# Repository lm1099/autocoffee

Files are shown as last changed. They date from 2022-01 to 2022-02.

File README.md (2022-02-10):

# SDP DT05 - AutoCoffee

## To-do
- Add power headers
- Layout main PCB
- Finish power PCB schematic

## Done
- Voltage regulators (12V to 5V, 3.3V)
- GPIO headers
- HM-10 BLE module
- LCD module
- DS3231 RTC module
- ISCP programming interface
- DS18B20 temp sensors (x2)
- VL6810X TOF sensors (x4)
- A4988 stepper motor drivers (x6)
- Fan driver (x1)

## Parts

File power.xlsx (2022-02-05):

Bus (V) | Current (A) | Qty | Total (A) | Power (W) | Part
3.3 | 0.5 | 1 | 0.5 | 1.65 | PIC24
3.3 | 0.05 | 1 | 0.05 | 0.165 | HM-10
15 | 0.05 | 1 | 0.05 | 0.75 | LCD
3.3 | 0.01 | 6 | 0.06 | 0.198 | A4988
3.3 | 0.015 | 2 | 0.03 | 0.099 | VL6180X
12 | 9.31392 | 3 | 27.94176 | 335.30112 | Stepper Motors (x6)
12 | 0.6 | 1 | 0.6 | 7.2 | Water pump
12 | 1 | 1 | 1 | 12 | Fan

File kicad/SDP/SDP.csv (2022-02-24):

Source: | C:\Users\Landon\Documents\University of Akron\SDP\autocoffee\kicad\SDP\SDP.kicad_sch
Date: | 2/22/2022 9:56:27 AM
Tool: | Eeschema (6.0.2)
Generator: | C:\Program Files\KiCad\6.0\bin\scripting\plugins/bom_csv_grouped_by_value_with_fp.py
Component Count: | 105
Ref | Qnty | Value | Cmp name | Footprint | Description | Vendor
B1, | 1 | 1056 | 1056 | Keystone_1056:1056
C1, C27, | 2 | 10u | C_Small | Capacitor_SMD:C_0805_2012Metric | Unpolarized capacitor, small symbol
C2, C3, C4, C5, C6, C7, | 6 | 0.1u | C_Small | Capacitor_SMD:C_0603_1608Metric | Unpolarized capacitor, small symbol
C8, C14, | 2 | 10u | C_Small | Capacitor_SMD:C_1206_3216Metric | Unpolarized capacitor, small symbol
C9, C15, C16, | 3 | 220p | C_Small | Capacitor_SMD:C_0805_2012Metric | Unpolarized capacitor, small symbol
C10, | 1 | 56p | C_Small | Capacitor_SMD:C_0805_2012Metric | Unpolarized capacitor, small symbol
C11, C17, | 2 | 0.015u | C_Small | Capacitor_SMD:C_0805_2012Metric | Unpolarized capacitor, small symbol
C12, C18, C22, C23, C26, | 5 | 0.1u | C_Small | Capacitor_SMD:C_0805_2012Metric | Unpolarized capacitor, small symbol
C13, | 1 | 330u | C_Polarized_Small_US | EEETG1C331UP:EEETG1C331UP | Polarized capacitor, small US symbol
C19, | 1 | 470u | C_Polarized_Small_US | EEVTG1C471Q:EEVTG1C471Q | Polarized capacitor, small US symbol
C20, C21, | 2 | 27p | C_Small | Capacitor_SMD:C_0805_2012Metric | Unpolarized capacitor, small symbol
C24, C25, | 2 | 15p | C_Small | Capacitor_SMD:C_0805_2012Metric | Unpolarized capacitor, small symbol
C39, | 1 | 47u | C_Small | Capacitor_THT:C_Radial_D8.0mm_H11.5mm_P3.50mm | Unpolarized capacitor, small symbol
C40, | 1 | 220u | C_Small | Capacitor_THT:C_Radial_D10.0mm_H16.0mm_P5.00mm | Unpolarized capacitor, small symbol
D1, D5, | 2 | Green | LED_Small | LED_SMD:LED_0805_2012Metric | Light emitting diode, small symbol
D2, | 1 | 1SMA5927BT3G | D_Zener_Small | Diode_SMD:D_SMA | Zener diode, small symbol
D3, D4, | 2 | CDBA240-G | D_Schottky_Small | Diode_SMD:D_SMA | Schottky diode, small symbol
F1, | 1 | 2A | Polyfuse_Small | Fuse:Fuse_1206_3216Metric | Resettable fuse, polymeric positive temperature coefficient, small symbol
H1, H2, H3, H4, | 4 | MountingHole_Pad | MountingHole_Pad | MountingHole:MountingHole_3.2mm_M3_Pad | Mounting Hole with connection
J1, | 1 | GPIO | Conn_02x07_Odd_Even | Connector_PinSocket_2.54mm:PinSocket_2x07_P2.54mm_Vertical | Generic connector, double row, 02x07, odd/even pin numbering scheme (row 1 odd numbers, row 2 even numbers), script generated (kicad-library-utils/schlib/autogen/connector/)
J2, J13, J14, J15, J16, J17, | 6 | Conn_01x03 | Conn_01x03 | Connector_PinSocket_2.54mm:PinSocket_1x03_P2.54mm_Vertical | Generic connector, single row, 01x03, script generated (kicad-library-utils/schlib/autogen/connector/)
J3, | 1 | UART | Conn_02x04_Odd_Even | Connector_PinSocket_2.54mm:PinSocket_2x04_P2.54mm_Vertical | Generic connector, double row, 02x04, odd/even pin numbering scheme (row 1 odd numbers, row 2 even numbers), script generated (kicad-library-utils/schlib/autogen/connector/)
J4, | 1 | I2C1 | Conn_01x02 | Connector_PinSocket_2.54mm:PinSocket_1x02_P2.54mm_Vertical | Generic connector, single row, 01x02, script generated (kicad-library-utils/schlib/autogen/connector/)
J5, J6, J25, | 3 | Conn_01x04 | Conn_01x04 | Connector_PinSocket_2.54mm:PinSocket_1x04_P2.54mm_Vertical | Generic connector, single row, 01x04, script generated (kicad-library-utils/schlib/autogen/connector/)
J7, | 1 | RJ25 | RJ25 | 5555165-1:TE_5555165-1 | RJ connector, 6P6C (6 positions 6 connected)
J8, J9, J11, J12, | 4 | Conn_01x07 | Conn_01x07 | Connector_PinSocket_2.54mm:PinSocket_1x07_P2.54mm_Vertical | Generic connector, single row, 01x07, script generated (kicad-library-utils/schlib/autogen/connector/)
J10, | 1 | Limit | Conn_02x06_Odd_Even | Connector_PinHeader_2.54mm:PinHeader_2x06_P2.54mm_Vertical | Generic connector, double row, 02x06, odd/even pin numbering scheme (row 1 odd numbers, row 2 even numbers), script generated (kicad-library-utils/schlib/autogen/connector/)
J18, | 1 | 12V | Conn_02x02_Odd_Even | Connector_PinSocket_2.54mm:PinSocket_2x02_P2.54mm_Vertical | Generic connector, double row, 02x02, odd/even pin numbering scheme (row 1 odd numbers, row 2 even numbers), script generated (kicad-library-utils/schlib/autogen/connector/)
J19, | 1 | I2C2 | Conn_01x02 | Connector_PinSocket_2.54mm:PinSocket_1x02_P2.54mm_Vertical | Generic connector, single row, 01x02, script generated (kicad-library-utils/schlib/autogen/connector/)
J20, | 1 | POWER | Conn_01x02 | Connector_PinSocket_2.54mm:PinSocket_1x02_P2.54mm_Vertical | Generic connector, single row, 01x02, script generated (kicad-library-utils/schlib/autogen/connector/)
J24, | 1 | POWER | Conn_02x07_Odd_Even | Connector_PinSocket_2.54mm:PinSocket_2x07_P2.54mm_Vertical | Generic connector, double row, 02x07, odd/even pin numbering scheme (row 1 odd numbers, row 2 even numbers), script generated (kicad-library-utils/schlib/autogen/connector/)
J26, | 1 | Conn_01x02 | Conn_01x02 | TerminalBlock_Phoenix:TerminalBlock_Phoenix_PT-1,5-2-5.0-H_1x02_P5.00mm_Horizontal | Generic connector, single row, 01x02, script generated (kicad-library-utils/schlib/autogen/connector/)
J27, | 1 | MOTOR | Conn_02x08_Odd_Even | Connector_PinSocket_2.54mm:PinSocket_2x08_P2.54mm_Vertical | Generic connector, double row, 02x08, odd/even pin numbering scheme (row 1 odd numbers, row 2 even numbers), script generated (kicad-library-utils/schlib/autogen/connector/)
L1, L3, | 2 | 22u | L_Small | DR125-220-R:DR125-220-R | Inductor, small symbol
L2, | 1 | 15u | L_Small | Inductor_SMD:L_12x12mm_H8mm | Inductor, small symbol
MOSFET1, | 1 | SSM3J334R_LFT | SSM3J334R_LFT | Package_TO_SOT_SMD:SOT-23
R1, R7, | 2 | 332k | R_Small | Resistor_SMD:R_0805_2012Metric | Resistor, small symbol
R2, R4, R16, R17, R20, R21, R22, R23, R24, R25, | 10 | 10k | R_Small | Resistor_SMD:R_0805_2012Metric | Resistor, small symbol
R3, R9, | 2 | 68.1k | R_Small | Resistor_SMD:R_0805_2012Metric | Resistor, small symbol
R5, | 1 | 1.91k | R_Small | Resistor_SMD:R_0805_2012Metric | Resistor, small symbol
R6, | 1 | 40.2k | R_Small | Resistor_SMD:R_0805_2012Metric | Resistor, small symbol
R8, | 1 | 10.2k | R_Small | Resistor_SMD:R_0805_2012Metric | Resistor, small symbol
R10, | 1 | 3.3k | R_Small | Resistor_SMD:R_0805_2012Metric | Resistor, small symbol
R11, | 1 | 30.9k | R_Small | Resistor_SMD:R_0805_2012Metric | Resistor, small symbol
R12, R13, R14, R15, R19, | 5 | 2k2 | R_Small | Resistor_SMD:R_0805_2012Metric | Resistor, small symbol
R18, R47, | 2 | 50k | R_Small | Resistor_SMD:R_0805_2012Metric | Resistor, small symbol
R48, | 1 | 1k | R_Small | Resistor_SMD:R_0805_2012Metric | Resistor, small symbol
R49, | 1 | 0.68 | R_Small | Resistor_SMD:R_0805_2012Metric | Resistor, small symbol
SW1, | 1 | SW_Push_Dual | SW_Push_Dual | 1825910-6:SW_1825910-6-4 | Push button switch, generic, symbol, four pins
TP1, TP2, | 2 | TestPoint_Small | TestPoint_Small | TestPoint:TestPoint_Keystone_5005-5009_Compact | test point
U1, U2, | 2 | TPS54233 | TPS54233 | Package_SO:SOIC-8_3.9x4.9mm_P1.27mm | 2A, Step Down DC-DC Converter with Eco-mode, 3.5-28V Input Voltage, SO-8
U3, | 1 | PIC24FJ128GA010-I/PT | PIC24FJ128GA010-I{slash}PT | PIC24FJ128GA010-I-PT:PIC24FJ128GA010-I&slash_PT
U4, | 1 | DS3231SN-T&R | DS3231SN-T&R_1 | DS3231SN:DS3231SN-T&R
Y1, | 1 | 8MHz | Crystal_Small | ECS-80-20-5PXDU-TR:XTAL_ECS-80-20-5PXDU-TR | Two pin crystal, small symbol
Y2, | 1 | 32.768kHz | Crystal_Small | Crystal:Crystal_DS26_D2.0mm_L6.0mm_Horizontal | Two pin crystal, small symbol

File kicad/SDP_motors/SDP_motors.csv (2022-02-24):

Source: | C:\Users\Landon\Documents\University of Akron\SDP\autocoffee\kicad\SDP_motors\SDP_motors.kicad_sch
Date: | 2/23/2022 13:58
Tool: | Eeschema (6.0.2)
Generator: | C:\Program Files\KiCad\6.0\bin\scripting\plugins/bom_csv_grouped_by_value_with_fp.py
Component Count: | 76
Ref | Qnty | Value | Cmp name | Footprint | Description | Vendor
A1, A2, A3, A4, A5, A6, | 6 | Pololu_Breakout_A4988 | Pololu_Breakout_A4988 | Module:Pololu_Breakout-16_15.2x20.3mm | Pololu Breakout Board, Stepper Driver A4988
C1, C2, C3, C4, C5, C6, | 6 | 50TZV100M8X10.5 | 50TZV100M8X10.5 | 50TZV100M8X10:50TZV100M8X10.5
C7, C8, C9, | 3 | 470u | C_Small | Capacitor_THT:C_Radial_D12.5mm_H20.0mm_P5.00mm | Unpolarized capacitor, small symbol
D1, D2, D3, | 3 | SS1200 | 1N4007 | Diode_SMD:D_SMA | 1000V 1A General Purpose Rectifier Diode, DO-41
H1, H2, H3, H4, | 4 | MountingHole_Pad | MountingHole_Pad | MountingHole:MountingHole_3.2mm_M3_Pad | Mounting Hole with connection
J1, J2, J3, J4, J5, J6, | 6 | Conn_01x04 | Conn_01x04 | Connector_PinHeader_2.54mm:PinHeader_1x04_P2.54mm_Vertical | Generic connector, single row, 01x04, script generated (kicad-library-utils/schlib/autogen/connector/)
J7, J8, J9, | 3 | Conn_01x02 | Conn_01x02 | TerminalBlock_Phoenix:TerminalBlock_Phoenix_PT-1,5-2-5.0-H_1x02_P5.00mm_Horizontal | Generic connector, single row, 01x02, script generated (kicad-library-utils/schlib/autogen/connector/)
J10, | 1 | MOTOR | Conn_02x08_Odd_Even | Connector_PinSocket_2.54mm:PinSocket_2x08_P2.54mm_Vertical | Generic connector, double row, 02x08, odd/even pin numbering scheme (row 1 odd numbers, row 2 even numbers), script generated (kicad-library-utils/schlib/autogen/connector/)
JP1, JP4, JP7, JP10, JP13, JP16, | 6 | JP_MS1 | Jumper_2_Open | Jumper:SolderJumper-2_P1.3mm_Open_RoundedPad1.0x1.5mm | Jumper, 2-pole, open
JP2, JP5, JP8, JP11, JP14, JP17, | 6 | JP_MS2 | Jumper_2_Open | Jumper:SolderJumper-2_P1.3mm_Open_RoundedPad1.0x1.5mm | Jumper, 2-pole, open
JP3, JP6, JP9, JP12, JP15, JP18, | 6 | JP_MS3 | Jumper_2_Open | Jumper:SolderJumper-2_P1.3mm_Open_RoundedPad1.0x1.5mm | Jumper, 2-pole, open
Q1, Q2, Q3, | 3 | IRLZ44N | IRLZ44N | Package_TO_SOT_SMD:TO-263-2 | 47A Id, 55V Vds, 22mOhm Rds Single N-Channel HEXFET Power MOSFET, TO-220AB
R1, R2, R3, R4, R7, R8, R9, R10, R13, R14, R15, R16, R19, R20, R21, | 15 | 10k | R_Small | Resistor_SMD:R_0805_2012Metric | Resistor, small symbol
R5, R6, R11, R12, R17, R18, | 6 | 100k | R_Small | Resistor_SMD:R_0805_2012Metric | Resistor, small symbol
TP1, TP2, | 2 | TestPoint_Small | TestPoint_Small | TestPoint:TestPoint_Keystone_5005-5009_Compact | test point

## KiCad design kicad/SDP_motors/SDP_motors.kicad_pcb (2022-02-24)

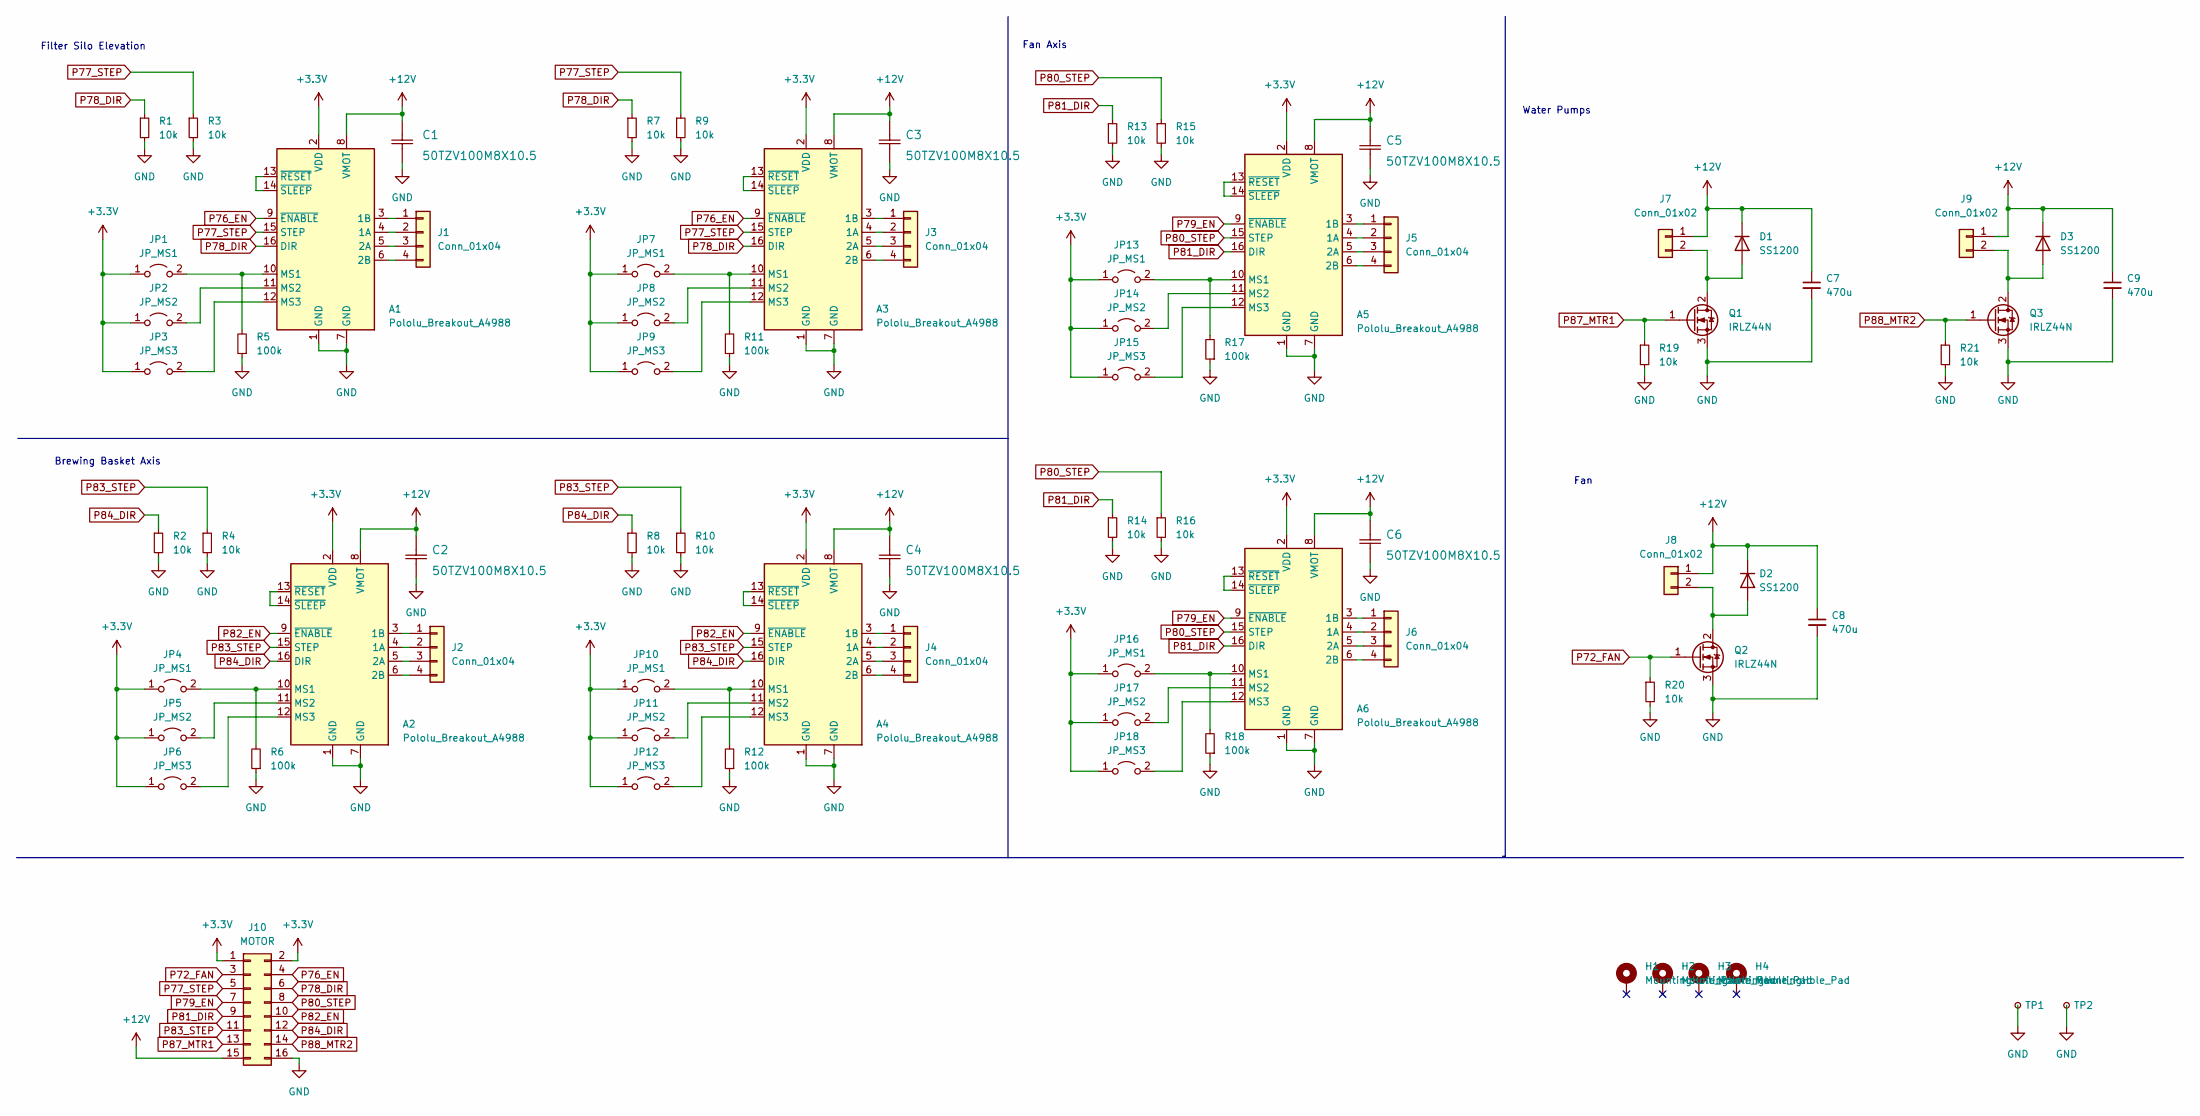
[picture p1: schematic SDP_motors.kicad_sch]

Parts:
A1, A2, A3, A4, A5, A6: Pololu_Breakout_A4988; Pololu_Breakout-16_15.2x20.3mm
C1, C2, C3, C4, C5, C6: 50TZV100M8X10.5
C7, C8, C9: 470u; C_Radial_D12.5mm_H20.0mm_P5.00mm
D1, D2, D3: SS1200; D_SMA
H1, H2, H3, H4: MountingHole_Pad; MountingHole_3.2mm_M3_Pad
J1, J2, J3, J4, J5, J6: Conn_01x04; PinHeader_1x04_P2.54mm_Vertical
J7, J8, J9: Conn_01x02; TerminalBlock_Phoenix_PT-1,5-2-5.0-H_1x02_P5.00mm_Horizontal
J10: MOTOR; PinSocket_2x08_P2.54mm_Vertical
JP1, JP4, JP7, JP10, JP13, JP16: JP_MS1; SolderJumper-2_P1.3mm_Open_RoundedPad1.0x1.5mm
JP2, JP5, JP8, JP11, JP14, JP17: JP_MS2; SolderJumper-2_P1.3mm_Open_RoundedPad1.0x1.5mm
JP3, JP6, JP9, JP12, JP15, JP18: JP_MS3; SolderJumper-2_P1.3mm_Open_RoundedPad1.0x1.5mm
Q1, Q2, Q3: IRLZ44N; TO-263-2
R1, R2, R3, R4, R7, R8, R9, R10, R13, R14, R15, R16, R19, R20, R21: 10k; R_0805_2012Metric
R5, R6, R11, R12, R17, R18: 100k; R_0805_2012Metric
TP1, TP2: TestPoint_Small; TestPoint_Keystone_5005-5009_Compact

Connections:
+3V3: A1.2 (VDD), A2.2 (VDD), A3.2 (VDD), A4.2 (VDD), A5.2 (VDD), A6.2 (VDD), J10.1, J10.2, JP1.1 (A), JP2.1 (A), JP3.1 (A), JP4.1 (A), JP5.1 (A), JP6.1 (A), JP7.1 (A), JP8.1 (A), JP9.1 (A), JP10.1 (A), JP11.1 (A), JP12.1 (A), JP13.1 (A), JP14.1 (A), JP15.1 (A), JP16.1 (A), JP17.1 (A), JP18.1 (A)
+12V: A1.8 (VMOT), A2.8 (VMOT), A3.8 (VMOT), A4.8 (VMOT), A5.8 (VMOT), A6.8 (VMOT), C1.2, C2.2, C3.2, C4.2, C5.2, C6.2, C7.1, C8.1, C9.1, D1.1 (K), D2.1 (K), D3.1 (K), J7.1, J8.1, J9.1, J10.15
GND: A1.1 (GND), A1.7 (GND), A2.1 (GND), A2.7 (GND), A3.1 (GND), A3.7 (GND), A4.1 (GND), A4.7 (GND), A5.1 (GND), A5.7 (GND), A6.1 (GND), A6.7 (GND), C1.1, C2.1, C3.1, C4.1, C5.1, C6.1, C7.2, C8.2, C9.2, J10.16, Q1.3 (S), Q2.3 (S), Q3.3 (S), R1.2, R2.2, R3.2, R4.2, R5.1, R6.1, R7.2, R8.2, R9.2, R10.2, R11.1, R12.1, R13.2, R14.2, R15.2, R16.2, R17.1, R18.1, R19.2, R20.2, R21.2, TP1.1, TP2.1
unnamed: A1.3 (1B), J1.1
unnamed: A1.4 (1A), J1.2
unnamed: A1.5 (2A), J1.3
unnamed: A1.6 (2B), J1.4
unnamed: A1.10 (MS1), JP1.2 (B), R5.2
unnamed: A1.11 (MS2), JP2.2 (B)
unnamed: A1.12 (MS3), JP3.2 (B)
unnamed: A1.13 (~RESET), A1.14 (~SLEEP)
unnamed: A2.3 (1B), J2.1
unnamed: A2.4 (1A), J2.2
unnamed: A2.5 (2A), J2.3
unnamed: A2.6 (2B), J2.4
unnamed: A2.10 (MS1), JP4.2 (B), R6.2
unnamed: A2.11 (MS2), JP5.2 (B)
unnamed: A2.12 (MS3), JP6.2 (B)
unnamed: A2.13 (~RESET), A2.14 (~SLEEP)
unnamed: A3.3 (1B), J3.1
unnamed: A3.4 (1A), J3.2
unnamed: A3.5 (2A), J3.3
unnamed: A3.6 (2B), J3.4
unnamed: A3.10 (MS1), JP7.2 (B), R11.2
unnamed: A3.11 (MS2), JP8.2 (B)
unnamed: A3.12 (MS3), JP9.2 (B)
unnamed: A3.13 (~RESET), A3.14 (~SLEEP)
unnamed: A4.3 (1B), J4.1
unnamed: A4.4 (1A), J4.2
unnamed: A4.5 (2A), J4.3
unnamed: A4.6 (2B), J4.4
unnamed: A4.10 (MS1), JP10.2 (B), R12.2
unnamed: A4.11 (MS2), JP11.2 (B)
unnamed: A4.12 (MS3), JP12.2 (B)
unnamed: A4.13 (~RESET), A4.14 (~SLEEP)
unnamed: A5.3 (1B), J5.1
unnamed: A5.4 (1A), J5.2
unnamed: A5.5 (2A), J5.3
unnamed: A5.6 (2B), J5.4
unnamed: A5.10 (MS1), JP13.2 (B), R17.2
unnamed: A5.11 (MS2), JP14.2 (B)
unnamed: A5.12 (MS3), JP15.2 (B)
unnamed: A5.13 (~RESET), A5.14 (~SLEEP)
unnamed: A6.3 (1B), J6.1
unnamed: A6.4 (1A), J6.2
unnamed: A6.5 (2A), J6.3
unnamed: A6.6 (2B), J6.4
unnamed: A6.10 (MS1), JP16.2 (B), R18.2
unnamed: A6.11 (MS2), JP17.2 (B)
unnamed: A6.12 (MS3), JP18.2 (B)
unnamed: A6.13 (~RESET), A6.14 (~SLEEP)
unnamed: D1.2 (A), J7.2, Q1.2 (D)
unnamed: D2.2 (A), J8.2, Q2.2 (D)
unnamed: D3.2 (A), J9.2, Q3.2 (D)
P72_FAN: J10.3, Q2.1 (G), R20.1
P76_EN: A1.9 (~ENABLE), A3.9 (~ENABLE), J10.4
P77_STEP: A1.15 (STEP), A3.15 (STEP), J10.5, R3.1, R9.1
P78_DIR: A1.16 (DIR), A3.16 (DIR), J10.6, R1.1, R7.1
P79_EN: A5.9 (~ENABLE), A6.9 (~ENABLE), J10.7
P80_STEP: A5.15 (STEP), A6.15 (STEP), J10.8, R15.1, R16.1
P81_DIR: A5.16 (DIR), A6.16 (DIR), J10.9, R13.1, R14.1
P82_EN: A2.9 (~ENABLE), A4.9 (~ENABLE), J10.10
P83_STEP: A2.15 (STEP), A4.15 (STEP), J10.11, R4.1, R10.1
P84_DIR: A2.16 (DIR), A4.16 (DIR), J10.12, R2.1, R8.1
P87_MTR1: J10.13, Q1.1 (G), R19.1
P88_MTR2: J10.14, Q3.1 (G), R21.1

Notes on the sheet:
Filter Silo Elevation
Water Pumps
Fan
Brewing Basket Axis
Fan Axis

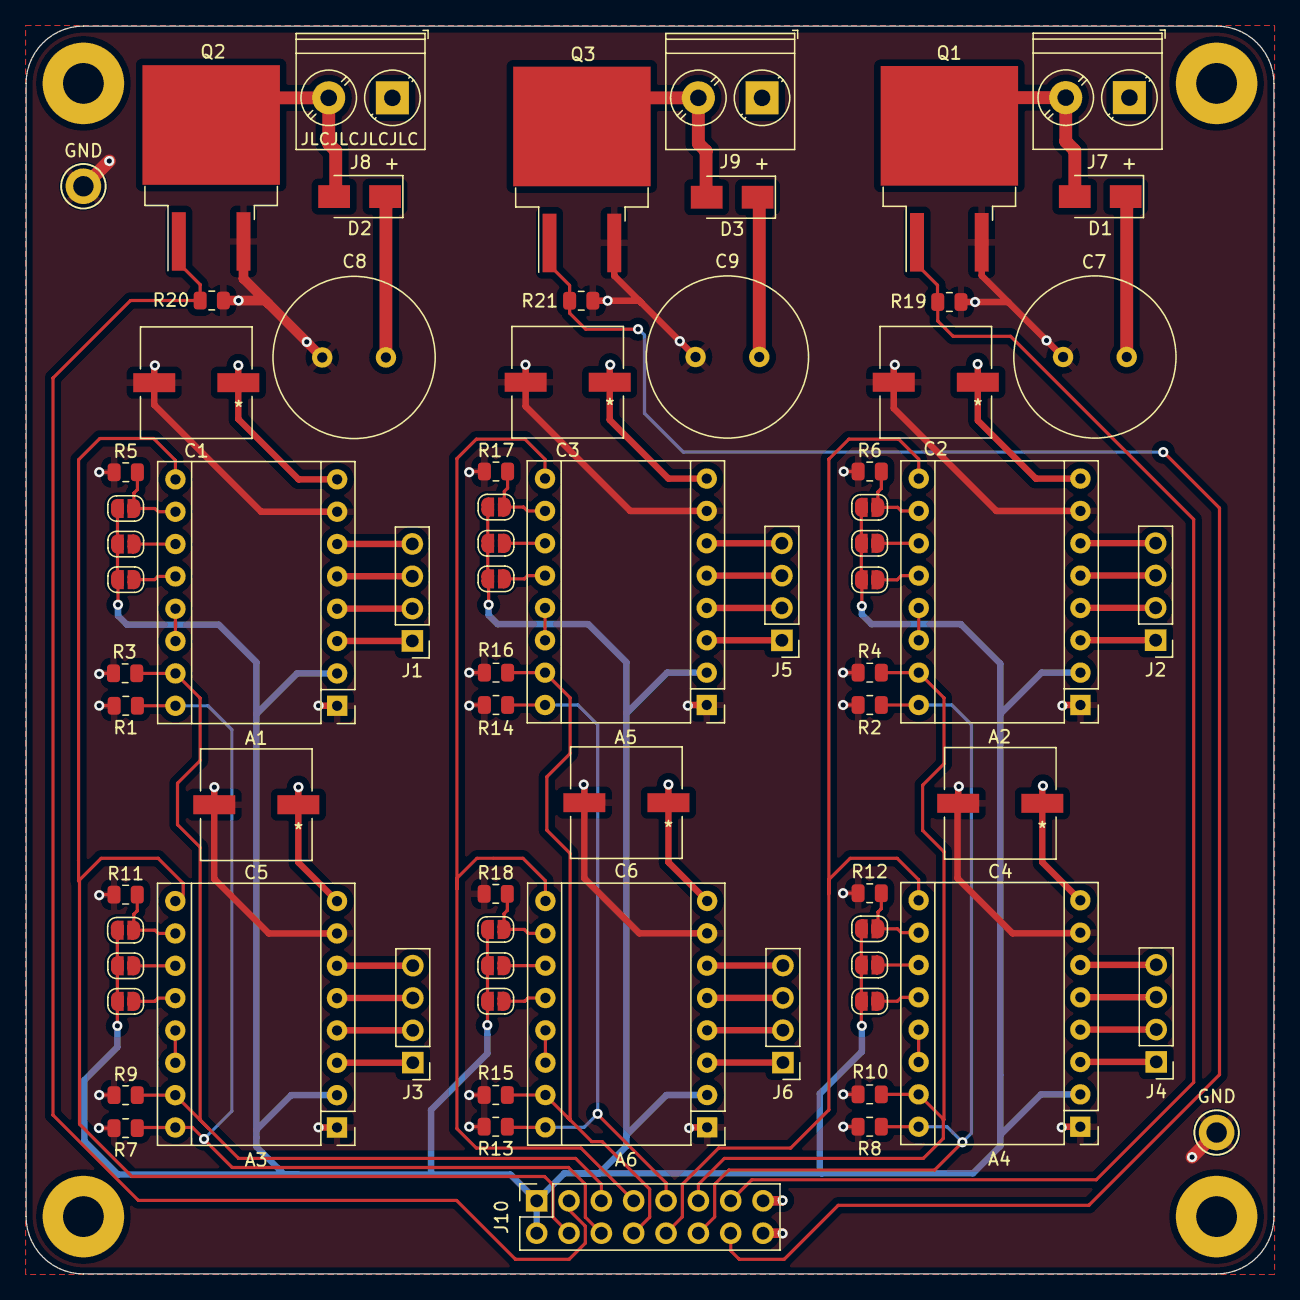
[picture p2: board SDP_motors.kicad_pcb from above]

Board: 4 copper layers, 98.0 x 98.0 mm, 76 parts (0 on the bottom side), 66 nets.

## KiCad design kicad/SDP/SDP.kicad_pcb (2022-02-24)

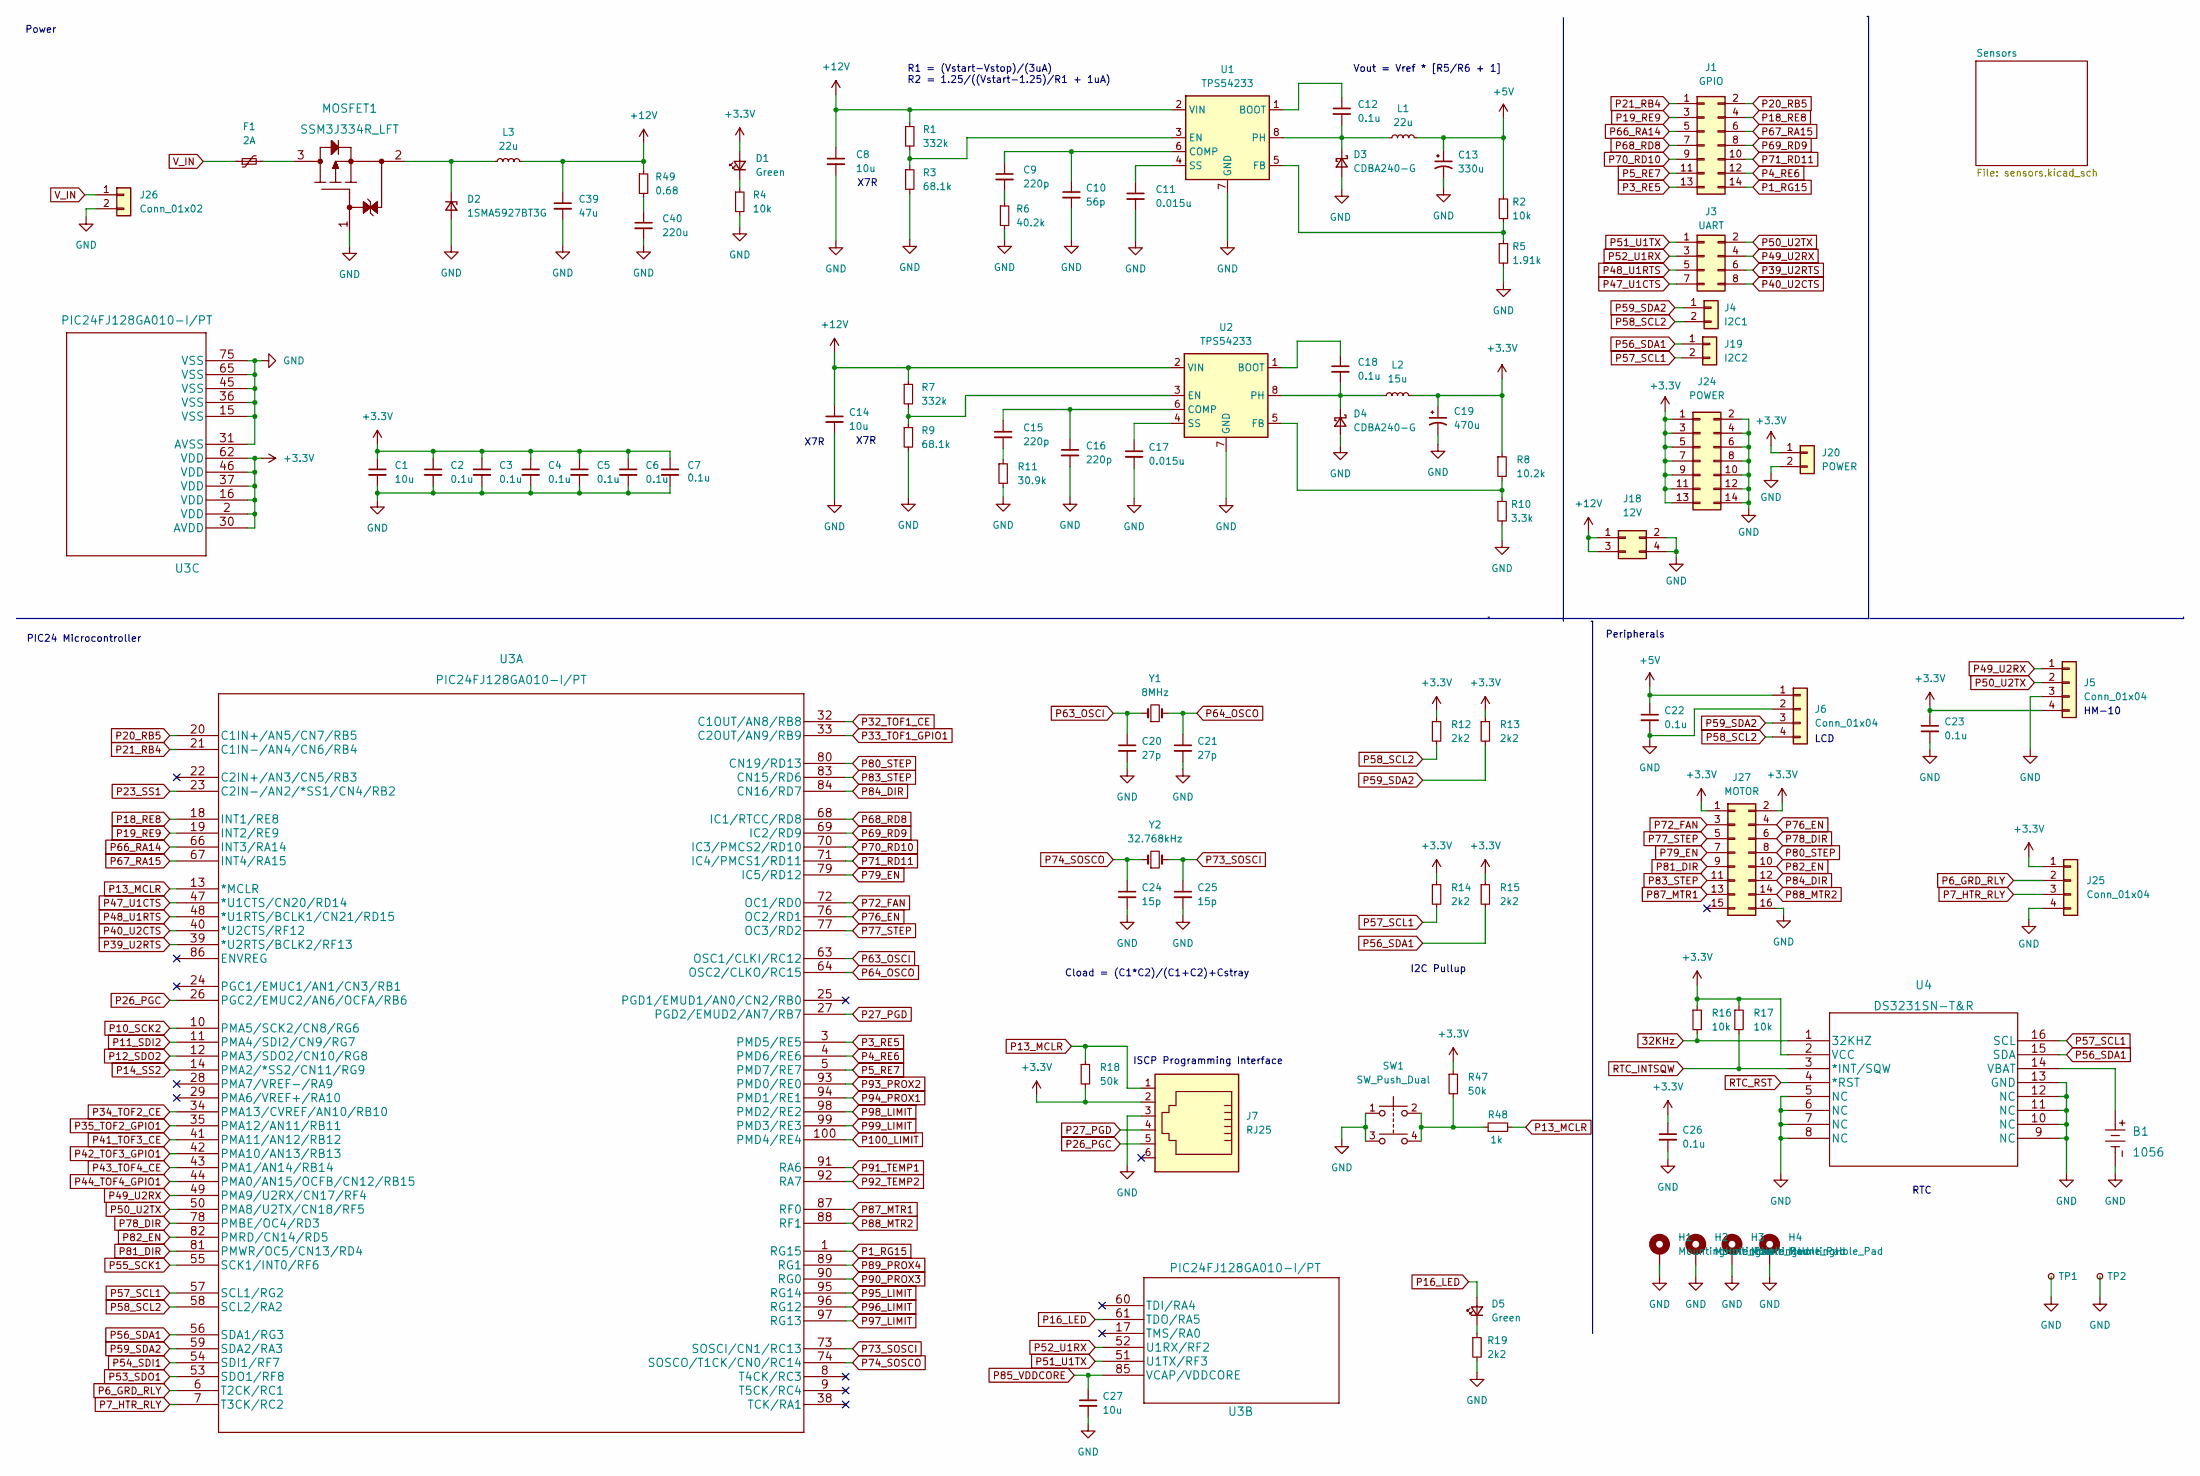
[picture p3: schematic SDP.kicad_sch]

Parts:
B1: 1056
C1, C27: 10u; C_0805_2012Metric
C2, C3, C4, C5, C6, C7: 0.1u; C_0603_1608Metric
C8, C14: 10u; C_1206_3216Metric
C9, C15, C16: 220p; C_0805_2012Metric
C10: 56p; C_0805_2012Metric
C11, C17: 0.015u; C_0805_2012Metric
C12, C18, C22, C23, C26: 0.1u; C_0805_2012Metric
C13: 330u; EEETG1C331UP
C19: 470u; EEVTG1C471Q
C20, C21: 27p; C_0805_2012Metric
C24, C25: 15p; C_0805_2012Metric
C39: 47u; C_Radial_D8.0mm_H11.5mm_P3.50mm
C40: 220u; C_Radial_D10.0mm_H16.0mm_P5.00mm
D1, D5: Green; LED_0805_2012Metric
D2: 1SMA5927BT3G; D_SMA
D3, D4: CDBA240-G; D_SMA
F1: 2A; Fuse_1206_3216Metric
H1, H2, H3, H4: MountingHole_Pad; MountingHole_3.2mm_M3_Pad
J1: GPIO; PinSocket_2x07_P2.54mm_Vertical
J3: UART; PinSocket_2x04_P2.54mm_Vertical
J4: I2C1; PinSocket_1x02_P2.54mm_Vertical
J5, J6, J25: Conn_01x04; PinSocket_1x04_P2.54mm_Vertical
J7: RJ25; TE_5555165-1
J18: 12V; PinSocket_2x02_P2.54mm_Vertical
J19: I2C2; PinSocket_1x02_P2.54mm_Vertical
J20: POWER; PinSocket_1x02_P2.54mm_Vertical
J24: POWER; PinSocket_2x07_P2.54mm_Vertical
J26: Conn_01x02; TerminalBlock_Phoenix_PT-1,5-2-5.0-H_1x02_P5.00mm_Horizontal
J27: MOTOR; PinSocket_2x08_P2.54mm_Vertical
L1, L3: 22u; DR125-220-R
L2: 15u; L_12x12mm_H8mm
MOSFET1: SSM3J334R_LFT; SOT-23
R1, R7: 332k; R_0805_2012Metric
R2, R4, R16, R17: 10k; R_0805_2012Metric
R3, R9: 68.1k; R_0805_2012Metric
R5: 1.91k; R_0805_2012Metric
R6: 40.2k; R_0805_2012Metric
R8: 10.2k; R_0805_2012Metric
R10: 3.3k; R_0805_2012Metric
R11: 30.9k; R_0805_2012Metric
R12, R13, R14, R15, R19: 2k2; R_0805_2012Metric
R18, R47: 50k; R_0805_2012Metric
R48: 1k; R_0805_2012Metric
R49: 0.68; R_0805_2012Metric
SW1: SW_Push_Dual; SW_1825910-6-4
TP1, TP2: TestPoint_Small; TestPoint_Keystone_5005-5009_Compact
U1, U2: TPS54233; SOIC-8_3.9x4.9mm_P1.27mm
U3: PIC24FJ128GA010-I/PT; PIC24FJ128GA010-I&slash_PT
U4: DS3231SN-T&R
Y1: 8MHz; XTAL_ECS-80-20-5PXDU-TR
Y2: 32.768kHz; Crystal_DS26_D2.0mm_L6.0mm_Horizontal

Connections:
32KHz: R16.2, U4.1 (32KHZ)
+3V3: C1.1, C2.1, C3.1, C4.1, C5.1, C6.1, C7.1, C19.1, C23.1, C26.1, D1.2 (A), J5.4, J7.2, J20.1, J24.1, J24.3, J24.5, J24.7, J24.9, J24.11, J24.13, J25.1, J27.1, J27.2, L2.2, R8.1, R12.1, R13.1, R14.1, R15.1, R16.1, R17.1, R18.2, R47.1, U3.2 (VDD), U3.16 (VDD), U3.30 (AVDD), U3.37 (VDD), U3.46 (VDD), U3.62 (VDD), U4.2 (VCC); also elsewhere on the board
+5V: C13.1, C22.1, J6.1, L1.2, R2.1
+12V: C8.1, C14.1, C39.1, J18.1, J18.3, L3.2, R1.1, R7.1, R49.1, U1.2 (VIN), U2.2 (VIN)
GND: B1.1, C1.2, C2.2, C3.2, C4.2, C5.2, C6.2, C7.2, C8.2, C10.2, C11.2, C13.2, C14.2, C16.2, C17.2, C19.2, C20.2, C21.2, C22.2, C23.2, C24.2, C25.2, C26.2, C27.2, C39.2, C40.2, D2.2 (A), D3.2 (A), D4.2 (A), H1.1, H2.1, H3.1, H4.1, J5.3, J6.2, J7.3, J18.2, J18.4, J20.2, J24.2, J24.4, J24.6, J24.8, J24.10, J24.12, J24.14, J25.4, J26.2, J27.16, MOSFET1.1 (GATE), R3.2, R4.2, R5.2, R6.2, R9.2, R10.2, R11.2, R19.2, SW1.1, SW1.3, TP1.1, TP2.1, U1.7 (GND), U2.7 (GND), U3.15 (VSS), U3.31 (AVSS), U3.36 (VSS), U3.45 (VSS), U3.65 (VSS), U3.75 (VSS), U4.5 (NC), U4.6 (NC), U4.7 (NC), U4.8 (NC), U4.9 (NC), U4.10 (NC), U4.11 (NC), U4.12 (NC), U4.13 (GND); also elsewhere on the board
unnamed: B1.2, U4.14 (VBAT)
unnamed: C9.2, R6.1
unnamed: C9.1, C10.1, U1.6 (COMP)
unnamed: C11.1, U1.4 (SS)
unnamed: C12.1, U1.1 (BOOT)
unnamed: C12.2, D3.1 (K), L1.1, U1.8 (PH)
unnamed: C15.1, C16.1, U2.6 (COMP)
unnamed: C15.2, R11.1
unnamed: C17.1, U2.4 (SS)
unnamed: C18.1, U2.1 (BOOT)
unnamed: C18.2, D4.1 (K), L2.1, U2.8 (PH)
unnamed: C40.1, R49.2
unnamed: D1.1 (K), R4.1
unnamed: D2.1 (K), L3.1, MOSFET1.2 (SOURCE)
unnamed: D5.1 (K), R19.1
unnamed: F1.2, MOSFET1.3 (DRAIN)
unnamed: R1.2, R3.1, U1.3 (EN)
unnamed: R2.2, R5.1, U1.5 (FB)
unnamed: R7.2, R9.1, U2.3 (EN)
unnamed: R8.2, R10.1, U2.5 (FB)
unnamed: R47.2, R48.1, SW1.2, SW1.4
P1_RG15: J1.14, U3.1 (RG15)
P3_RE5: J1.13, U3.3 (PMD5/RE5)
P4_RE6: J1.12, U3.4 (PMD6/RE6)
P5_RE7: J1.11, U3.5 (PMD7/RE7)
P6_GRD_RLY: J25.2, U3.6 (T2CK/RC1)
P7_HTR_RLY: J25.3, U3.7 (T3CK/RC2)
P10_SCK2: U3.10 (PMA5/SCK2/CN8/RG6)
P11_SDI2: U3.11 (PMA4/SDI2/CN9/RG7)
P12_SDO2: U3.12 (PMA3/SDO2/CN10/RG8)
P13_MCLR: J7.1, R18.1, R48.2, U3.13 (*MCLR)
P14_SS2: U3.14 (PMA2/*SS2/CN11/RG9)
P16_LED: D5.2 (A), U3.61 (TDO/RA5)
P18_RE8: J1.4, U3.18 (INT1/RE8)
P19_RE9: J1.3, U3.19 (INT2/RE9)
P20_RB5: J1.2, U3.20 (C1IN+/AN5/CN7/RB5)
P21_RB4: J1.1, U3.21 (C1IN-/AN4/CN6/RB4)
P23_SS1: U3.23 (C2IN-/AN2/*SS1/CN4/RB2)
P26_PGC: J7.5, U3.26 (PGC2/EMUC2/AN6/OCFA/RB6)
P27_PGD: J7.4, U3.27 (PGD2/EMUD2/AN7/RB7)
P32_TOF1_CE: U3.32 (C1OUT/AN8/RB8); also elsewhere on the board
P33_TOF1_GPIO1: U3.33 (C2OUT/AN9/RB9); also elsewhere on the board
P34_TOF2_CE: U3.34 (PMA13/CVREF/AN10/RB10); also elsewhere on the board
P35_TOF2_GPIO1: U3.35 (PMA12/AN11/RB11); also elsewhere on the board
P39_U2RTS: J3.6, U3.39 (*U2RTS/BCLK2/RF13)
P40_U2CTS: J3.8, U3.40 (*U2CTS/RF12)
P41_TOF3_CE: U3.41 (PMA11/AN12/RB12); also elsewhere on the board
P42_TOF3_GPIO1: U3.42 (PMA10/AN13/RB13); also elsewhere on the board
P43_TOF4_CE: U3.43 (PMA1/AN14/RB14); also elsewhere on the board
P44_TOF4_GPIO1: U3.44 (PMA0/AN15/OCFB/CN12/RB15); also elsewhere on the board
P47_U1CTS: J3.7, U3.47 (*U1CTS/CN20/RD14)
P48_U1RTS: J3.5, U3.48 (*U1RTS/BCLK1/CN21/RD15)
P49_U2RX: J3.4, J5.1, U3.49 (PMA9/U2RX/CN17/RF4)
P50_U2TX: J3.2, J5.2, U3.50 (PMA8/U2TX/CN18/RF5)
P51_U1TX: J3.1, U3.51 (U1TX/RF3)
P52_U1RX: J3.3, U3.52 (U1RX/RF2)
P53_SDO1: U3.53 (SDO1/RF8)
P54_SDI1: U3.54 (SDI1/RF7)
P55_SCK1: U3.55 (SCK1/INT0/RF6)
P56_SDA1: J19.1, R15.2, U3.56 (SDA1/RG3), U4.15 (SDA); also elsewhere on the board
P57_SCL1: J19.2, R14.2, U3.57 (SCL1/RG2), U4.16 (SCL); also elsewhere on the board
P58_SCL2: J4.2, J6.4, R12.2, U3.58 (SCL2/RA2); also elsewhere on the board
P59_SDA2: J4.1, J6.3, R13.2, U3.59 (SDA2/RA3); also elsewhere on the board
P63_OSCI: C20.1, U3.63 (OSC1/CLKI/RC12), Y1.1
P64_OSCO: C21.1, U3.64 (OSC2/CLKO/RC15), Y1.2
P66_RA14: J1.5, U3.66 (INT3/RA14)
P67_RA15: J1.6, U3.67 (INT4/RA15)
P68_RD8: J1.7, U3.68 (IC1/RTCC/RD8)
P69_RD9: J1.8, U3.69 (IC2/RD9)
P70_RD10: J1.9, U3.70 (IC3/PMCS2/RD10)
P71_RD11: J1.10, U3.71 (IC4/PMCS1/RD11)
P72_FAN: J27.3, U3.72 (OC1/RD0)
P73_SOSCI: C25.1, U3.73 (SOSCI/CN1/RC13), Y2.2
P74_SOSCO: C24.1, U3.74 (SOSCO/T1CK/CN0/RC14), Y2.1
P76_EN: J27.4, U3.76 (OC2/RD1)
P77_STEP: J27.5, U3.77 (OC3/RD2)
P78_DIR: J27.6, U3.78 (PMBE/OC4/RD3)
P79_EN: J27.7, U3.79 (IC5/RD12)
P80_STEP: J27.8, U3.80 (CN19/RD13)
P81_DIR: J27.9, U3.81 (PMWR/OC5/CN13/RD4)
P82_EN: J27.10, U3.82 (PMRD/CN14/RD5)
P83_STEP: J27.11, U3.83 (CN15/RD6)
P84_DIR: J27.12, U3.84 (CN16/RD7)
P85_VDDCORE: C27.1, U3.85 (VCAP/VDDCORE)
P87_MTR1: J27.13, U3.87 (RF0)
P88_MTR2: J27.14, U3.88 (RF1)
P89_PROX4: U3.89 (RG1); also elsewhere on the board
P90_PROX3: U3.90 (RG0); also elsewhere on the board
P91_TEMP1: U3.91 (RA6); also elsewhere on the board
P92_TEMP2: U3.92 (RA7); also elsewhere on the board
P93_PROX2: U3.93 (PMD0/RE0); also elsewhere on the board
P94_PROX1: U3.94 (PMD1/RE1); also elsewhere on the board
P95_LIMIT: U3.95 (RG14); also elsewhere on the board
P96_LIMIT: U3.96 (RG12); also elsewhere on the board
P97_LIMIT: U3.97 (RG13); also elsewhere on the board
P98_LIMIT: U3.98 (PMD2/RE2); also elsewhere on the board
P99_LIMIT: U3.99 (PMD3/RE3); also elsewhere on the board
P100_LIMIT: U3.100 (PMD4/RE4); also elsewhere on the board
RTC_INTSQW: R17.2, U4.3 (*INT/SQW)
RTC_RST: U4.4 (*RST)
V_IN: F1.1, J26.1

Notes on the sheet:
RTC
X7R
HM-10
Peripherals
R1 = (Vstart-Vstop)/(3uA) R2 = 1.25/((Vstart-1.25)/R1 + 1uA)
I2C Pullup
ISCP Programming Interface
Power
Cload = (C1*C2)/(C1+C2)+Cstray
LCD
PIC24 Microcontroller
Vout = Vref * [R5/R6 + 1]

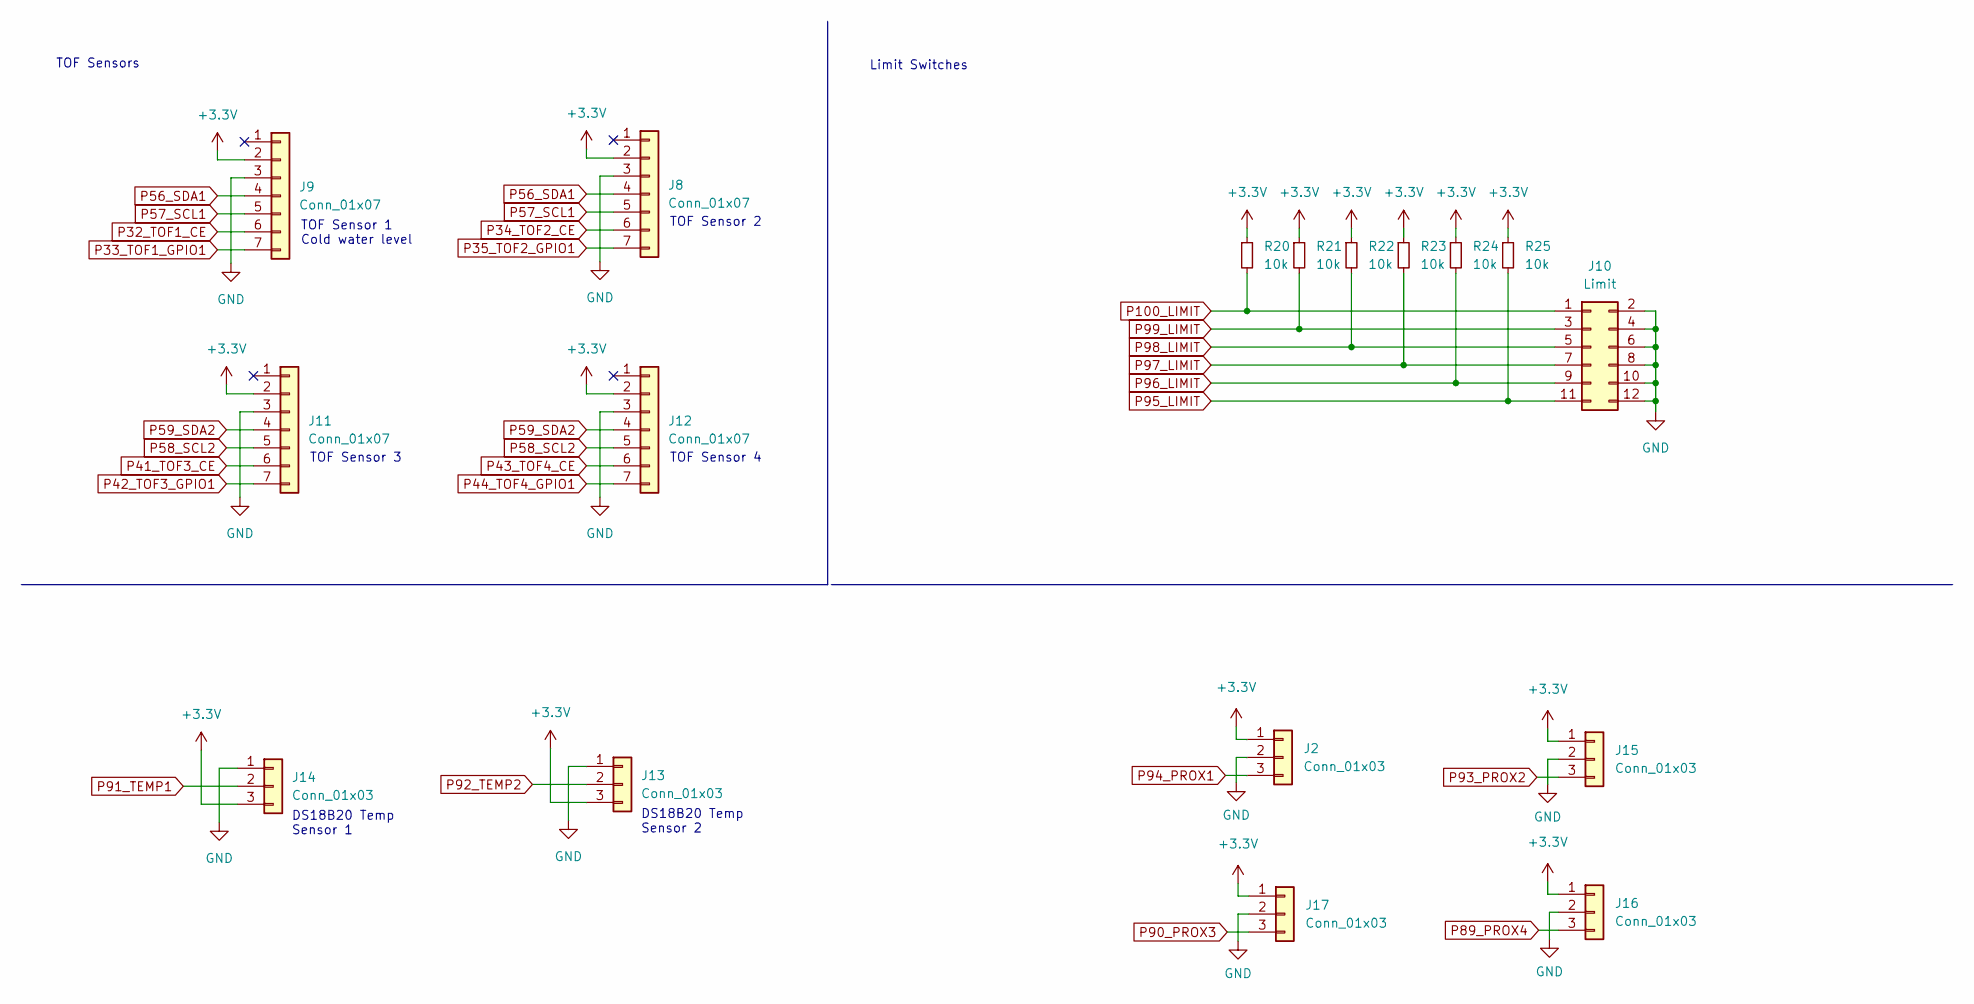
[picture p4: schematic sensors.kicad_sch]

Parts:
J2, J13, J14, J15, J16, J17: Conn_01x03; PinSocket_1x03_P2.54mm_Vertical
J8, J9, J11, J12: Conn_01x07; PinSocket_1x07_P2.54mm_Vertical
J10: Limit; PinHeader_2x06_P2.54mm_Vertical
R20, R21, R22, R23, R24, R25: 10k; R_0805_2012Metric

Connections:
+3V3: J2.1, J8.2, J9.2, J11.2, J12.2, J13.3, J14.3, J15.1, J16.1, J17.1, R20.1, R21.1, R22.1, R23.1, R24.1, R25.1; also elsewhere on the board
GND: J2.2, J8.3, J9.3, J10.2, J10.4, J10.6, J10.8, J10.10, J10.12, J11.3, J12.3, J13.1, J14.1, J15.2, J16.2, J17.2; also elsewhere on the board
P32_TOF1_CE: J9.6; also elsewhere on the board
P33_TOF1_GPIO1: J9.7; also elsewhere on the board
P34_TOF2_CE: J8.6; also elsewhere on the board
P35_TOF2_GPIO1: J8.7; also elsewhere on the board
P41_TOF3_CE: J11.6; also elsewhere on the board
P42_TOF3_GPIO1: J11.7; also elsewhere on the board
P43_TOF4_CE: J12.6; also elsewhere on the board
P44_TOF4_GPIO1: J12.7; also elsewhere on the board
P56_SDA1: J8.4, J9.4; also elsewhere on the board
P57_SCL1: J8.5, J9.5; also elsewhere on the board
P58_SCL2: J11.5, J12.5; also elsewhere on the board
P59_SDA2: J11.4, J12.4; also elsewhere on the board
P89_PROX4: J16.3; also elsewhere on the board
P90_PROX3: J17.3; also elsewhere on the board
P91_TEMP1: J14.2; also elsewhere on the board
P92_TEMP2: J13.2; also elsewhere on the board
P93_PROX2: J15.3; also elsewhere on the board
P94_PROX1: J2.3; also elsewhere on the board
P95_LIMIT: J10.11, R25.2; also elsewhere on the board
P96_LIMIT: J10.9, R24.2; also elsewhere on the board
P97_LIMIT: J10.7, R23.2; also elsewhere on the board
P98_LIMIT: J10.5, R22.2; also elsewhere on the board
P99_LIMIT: J10.3, R21.2; also elsewhere on the board
P100_LIMIT: J10.1, R20.2; also elsewhere on the board

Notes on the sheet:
TOF Sensor 4
TOF Sensors
TOF Sensor 1 Cold water level
TOF Sensor 2
TOF Sensor 3
DS18B20 Temp Sensor 2
DS18B20 Temp Sensor 1
Limit Switches

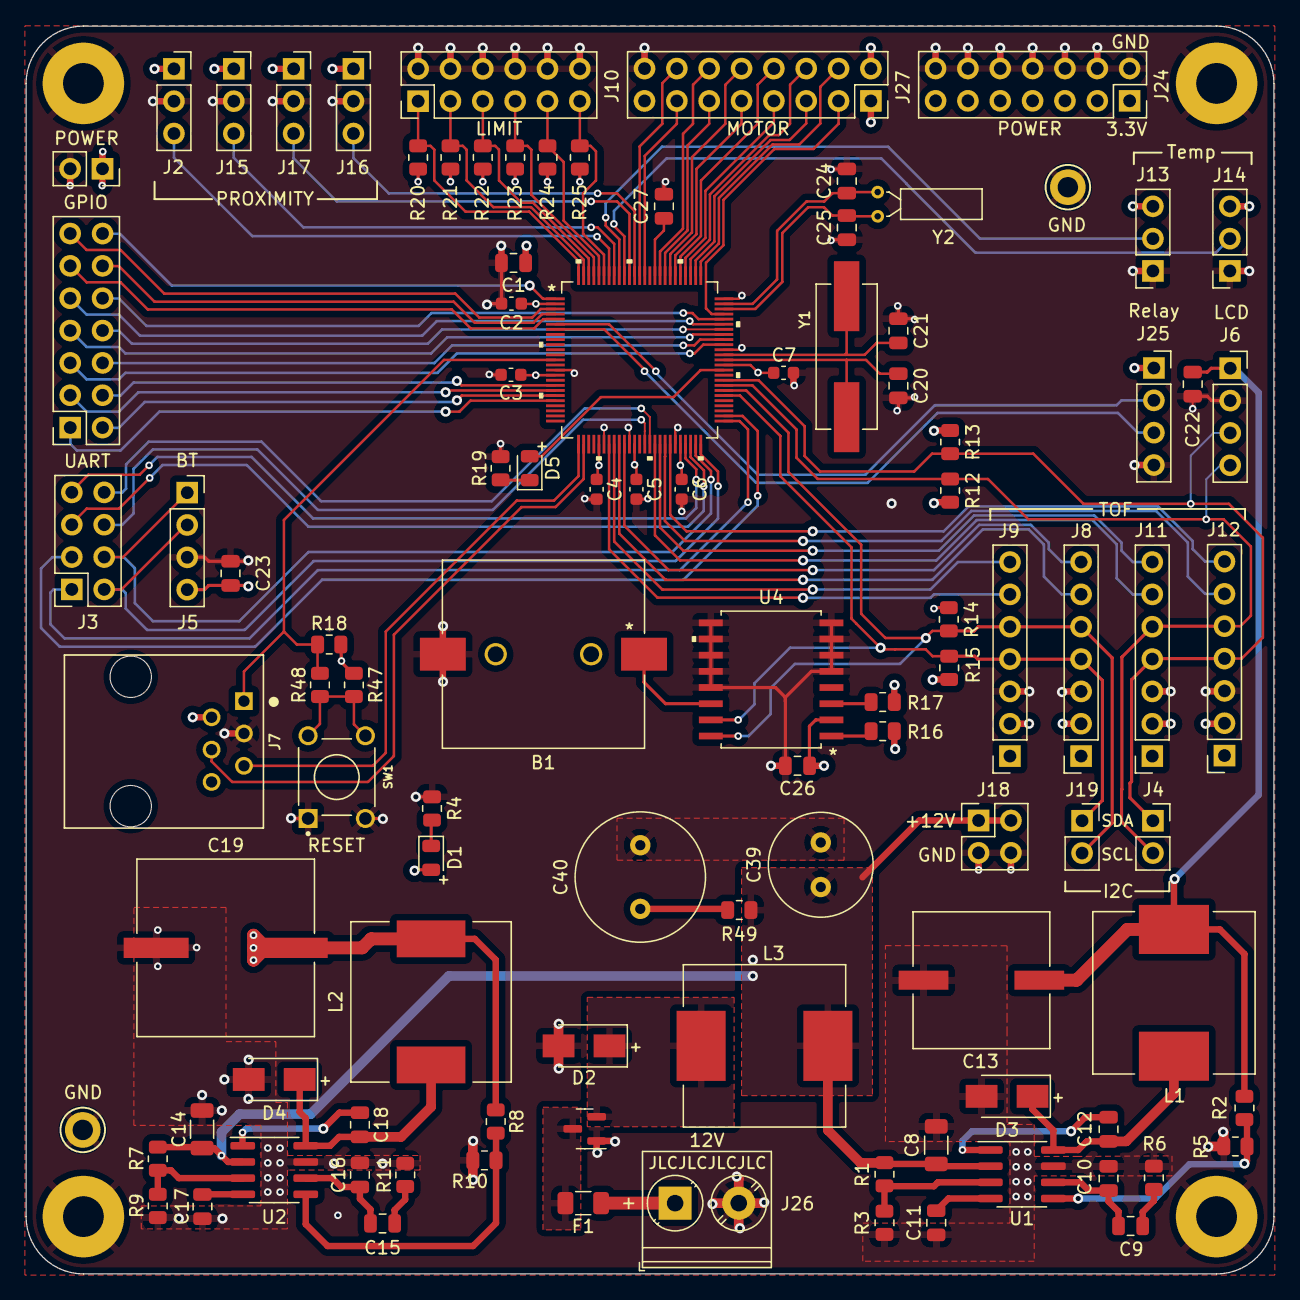
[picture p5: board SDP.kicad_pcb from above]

Board: 4 copper layers, 98.0 x 98.0 mm, 105 parts (0 on the bottom side), 97 nets.

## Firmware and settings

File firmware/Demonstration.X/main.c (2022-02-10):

#include "mcc_generated_files/system.h"

#define DIRECTION_CCW 1
#define DIRECTION_CW 0

#define MAX(x, y) ((x > y) ? x : y)
#define CONSTRAIN(amt,low,high) ((amt)<(low)?(low):((amt)>(high)?(high):(amt)))
#define ABS(x) ((x)>0?(x):-(x))
#define TIMEDIFF(current, old) (((current < old) ? (unsigned long)1 << 16 : 0) + (unsigned long)current - (unsigned long)old)
#define TIMER (TMR2 + (TMR3HLD << 8))

typedef struct {
    uint16_t *portPtr;
    int stepPin;
    int dirPin;
    unsigned long stepInterval; // Current interval between steps in microseconds
    unsigned long lastStepTime; // Last step time in microseconds
    float speed;    // Steps per second
    float maxSpeed; // Max speed in steps per second
    float acceleration; // Acceleration is steps per second per second
    int direction;  // 1 == CCW
    long targetPos;     // Steps
    long currentPos;    // Steps
    unsigned int minPulseWidth; // Minimum pulse width in microseconds
    
    long n;     // Step counter for speed calculations
    float c0;   // Initial step size in microseconds
    float cn;   // Last step size in microseconds
    float cmin; // Min step size in microseconds at max speed 
} stepper;

int direction = 1;
int targetPos = 0;

void initStepper(stepper *stepperInst, int stepperPin, int directionPin)
{
    stepperInst->dirPin = directionPin;
    stepperInst->stepPin = stepperPin;
    stepperInst->currentPos = 0;
    stepperInst->targetPos = 0;
    stepperInst->speed = 0.0;
    stepperInst->maxSpeed = 10.0;
    stepperInst->acceleration = 0.0;
    stepperInst->stepInterval = 0;
    stepperInst->minPulseWidth = 1;
    stepperInst->lastStepTime = 0;
    stepperInst->n = 0;
    stepperInst->c0 = 0.0;
    stepperInst->cn = 0.0;
    stepperInst->cmin = 1.0;
    stepperInst->direction = DIRECTION_CCW;
}

long distanceToGo(stepper *stepperInst)
{
    return stepperInst->targetPos - stepperInst->currentPos;
}

void setSpeed(stepper *stepperInst, float speed)
{
    if (speed == stepperInst->speed)
        return;
    speed = CONSTRAIN(speed, -stepperInst->maxSpeed, stepperInst->maxSpeed);
    if (speed == 0.0)
        stepperInst->stepInterval = 0;
    else
    {
        stepperInst->stepInterval = ABS(1000000.0 / speed);
        stepperInst->direction = (speed > 0.0) ? DIRECTION_CW : DIRECTION_CCW;
    }
    stepperInst->speed = speed;
}

void computeNewSpeed(stepper *stepperInst)
{
    long distanceTo = distanceToGo(stepperInst);
    long stepsToStop = (long)((stepperInst->speed * stepperInst->speed) / (2.0 * stepperInst->acceleration)); // Equation 16
    
    if (distanceTo == 0 && stepsToStop <= 1)
    {
        stepperInst->stepInterval = 0;
        stepperInst->speed = 0.0;
        stepperInst->n = 0;
        return;
    }
    
    if (distanceTo > 0)
    {
        // We are anticlockwise from the target
        // Need to go clockwise from here, maybe decelerate now
        if (stepperInst->n > 0)
        {
            // Currently accelerating, need to decel now? Or maybe going the wrong way?
            if ((stepsToStop >= distanceTo) || stepperInst->direction == DIRECTION_CCW)
                stepperInst->n = -stepsToStop; // Start deceleration
        }
        else if (stepperInst->n < 0)
        {
            // Currently decelerating, need to accel again?
            if ((stepsToStop < distanceTo) && stepperInst->direction == DIRECTION_CW)
                stepperInst->n = -stepperInst->n; // Start acceleration
        }
    }
    else if (distanceTo < 0)
    {
        // We are clockwise from the target
        // Need to go anticlockwise from here, maybe decelerate
        if (stepperInst->n > 0)
        {
            // Currently accelerating, need to decel now? Or maybe going the wrong way?
            if ((stepsToStop >= -distanceTo) || stepperInst->direction == DIRECTION_CW)
            stepperInst->n = -stepsToStop; // Start deceleration
        }
        else if (stepperInst->n < 0)
        {
            // Currently decelerating, need to accel again?
            if ((stepsToStop < -distanceTo) && stepperInst->direction == DIRECTION_CCW)
            stepperInst->n = -stepperInst->n; // Start accceleration
        }
    }
    
    // Need to accelerate or decelerate
    if (stepperInst->n == 0)
    {
        // First step from stopped
        stepperInst->cn = stepperInst->c0;
        stepperInst->direction = (distanceTo > 0) ? DIRECTION_CW : DIRECTION_CCW;
    }
    else
    {
        // Subsequent step. Works for accel (n is +_ve) and decel (n is -ve).
        stepperInst->cn = stepperInst->cn - ((2.0 * stepperInst->cn) / ((4.0 * stepperInst->n) + 1)); // Equation 13
        stepperInst->cn = MAX(stepperInst->cn, stepperInst->cmin); 
    }
    stepperInst->n++;
    stepperInst->stepInterval = stepperInst->cn;
    stepperInst->speed = 1000000.0 / stepperInst->cn;
    if (stepperInst->direction == DIRECTION_CCW)
        stepperInst->speed = -stepperInst->speed;
}

void setMaxSpeed(stepper *stepperInst, float speed)
{
    if (speed < 0.0)
       speed = -speed;
    if (stepperInst->maxSpeed != speed)
    {
        stepperInst->maxSpeed = speed;
        stepperInst->cmin = 1000000.0 / speed;
            // Recompute _n from current speed and adjust speed if accelerating or cruising
        if (stepperInst->n > 0)
        {
            stepperInst->n = (long)((stepperInst->speed * stepperInst->speed) / (2.0 * stepperInst->acceleration)); // Equation 16
            computeNewSpeed(stepperInst);
        }
    }
}

void moveTo(stepper *stepperInst, long absolute)
{
    if (stepperInst->targetPos != absolute)
    {
        stepperInst->targetPos = absolute;
        computeNewSpeed(stepperInst);
    }
}

void setOutputPins(stepper *stepperInst, int dirState, int stepState)
{
    if(stepState)
        *(stepperInst->portPtr) |= (1 << stepperInst->stepPin);
    else
        *(stepperInst->portPtr) &= ~(1 << stepperInst->stepPin);
    
    if(dirState)
        *(stepperInst->portPtr) |= (1 << stepperInst->dirPin);
    else
        *(stepperInst->portPtr) &= ~(1 << stepperInst->dirPin);
}

void step(stepper *stepperInst, long step)
{
    // _pin[0] is step, _pin[1] is direction
    setOutputPins(stepperInst, stepperInst->direction, 0); // Set direction first else get rogue pulses
    setOutputPins(stepperInst, stepperInst->direction, 1); // step HIGH
    // Caution 200ns setup time 
    // Delay the minimum allowed pulse width
    unsigned long  startTime = ((unsigned long)TIMER)*16;
    while(TIMEDIFF((unsigned long)TIMER*16, startTime) < stepperInst->minPulseWidth)
        continue;
    setOutputPins(stepperInst, stepperInst->direction, 0); // step LOW
}

int runSpeed(stepper *stepperInst)
{
    // Don't do anything unless we actually have a step interval
    if (!stepperInst->stepInterval)
        return 0;

    unsigned long currentTime = ((unsigned long)TIMER)*16;   // Get time in microseconds
    if (TIMEDIFF(currentTime, stepperInst->lastStepTime) >= stepperInst->stepInterval)
    {
        if (stepperInst->direction == DIRECTION_CW)
        {
            // Clockwise
            stepperInst->currentPos += 1;
        }
        else
        {
            // Anticlockwise  
            stepperInst->currentPos -= 1;
        }
        step(stepperInst, stepperInst->currentPos);

        stepperInst->lastStepTime = currentTime; // Caution: does not account for costs in step()

        return 1;
    }
    else
        return 0;
}

int run(stepper *stepperInst)
{
    if (runSpeed(stepperInst))
	computeNewSpeed(stepperInst);
    return stepperInst->speed != 0.0 || distanceToGo(stepperInst) != 0;
}

int i;
int buttonState;
int previousButtonState = 0;
int stepperEnable = 0;
int proximityState;
int previousProximityState = 0;
int switchState;
int previousSwitchState = 0;
int stepperSpeed = 100;
int fanButtonState, motorButtonState, heatingButtonState;

int main(void)
{
    // initialize the device
    SYSTEM_Initialize();
    
    T2CON = 0x00;   // Stops any 16/32-bit Timer2 operation
    T3CON = 0x00;   // Stops any 16-bit Timer3 operation
    TMR3 = 0x00;    // Clear contents of the timer3 register
    TMR2 = 0x00;    // Clear contents of the timer2 register
    PR3 = 0xFFFF;   // Load the Period register3 with the value 0xFFFF
    PR2 = 0xFFFF;   // Load the Period register2 with the value 0xFFFF
    T2CON = 0x8034;     // 1:256 prescaling, 32 bit operation (0b1000 0000 0011 1000)
    
    TRISF = 0x0000;     // Set all pins of PORTF as outputs
    TRISA = 0xFFF0;     // Set PORTA as outputs
    TRISDbits.TRISD6 = 1;   // Enable the button to toggle motor state
    TRISGbits.TRISG1 = 1;   // Enable the switch (active low) as an input
    TRISDbits.TRISD4 = 1;   // Enable the proximity sensor (active high) as an input
    TRISDbits.TRISD7 = 1;   // Enable the button to turn on fan
    TRISAbits.TRISA7 = 1;   // Enable the button to turn on grinding motor
    TRISDbits.TRISD13 = 1;  // Enable the button to turn on the heating element
    
    stepper Stepper1;
    initStepper(&Stepper1, 0, 1);
    Stepper1.portPtr = &PORTF;
    
    stepper Stepper2;
    initStepper(&Stepper2, 2, 3);
    Stepper2.portPtr = &PORTF;
    
    setMaxSpeed(&Stepper1, 800);
    setSpeed(&Stepper1, 100);
    setMaxSpeed(&Stepper2, 800);
    setSpeed(&Stepper2, 100);
    while (1)
    {
        buttonState = PORTDbits.RD6;
        if (buttonState != previousButtonState && buttonState == 0) {               
            stepperEnable = !stepperEnable;     // Toggle stepper enable
            PORTAbits.RA3 = !stepperEnable;
        }
        previousButtonState = buttonState; // set previous button state
        
        proximityState = !PORTDbits.RD4;
        switchState = !PORTGbits.RG1;
        if ((proximityState != previousProximityState && proximityState == 1) || (switchState != previousSwitchState && switchState == 1))
        {
            stepperEnable = 0;
            PORTAbits.RA3 = !stepperEnable;
            stepperSpeed = -stepperSpeed;
            setSpeed(&Stepper1, stepperSpeed);        
            setSpeed(&Stepper2, stepperSpeed);
        }
        previousProximityState = proximityState; // set previous button state
        previousSwitchState = switchState; // set previous button state
        
        heatingButtonState = PORTDbits.RD13;
        if (heatingButtonState == 0)    // If the button is pressed
            PORTAbits.RA0 = 1;      // Turn on heating element
        else
            PORTAbits.RA0 = 0;      // Turn off heating element
        
        motorButtonState = PORTAbits.RA7;
        if (motorButtonState == 0)  // If the button is pressed
            PORTAbits.RA1 = 1;      // Turn on motor 
        else
            PORTAbits.RA1 = 0;      // Turn off motor
        
        fanButtonState = PORTDbits.RD7;
        if (fanButtonState == 0)    // If the button is pressed
            PORTAbits.RA2 = 1;      // Turn on fan
        else
            PORTAbits.RA2 = 0;      // Turn off fan
        
        if (stepperEnable == 1)
        {
            runSpeed(&Stepper1);    // Move if needed
            runSpeed(&Stepper2);    // Move if needed
        }
    }

    return 1;
}

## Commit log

2022-01-26 Added PIC24 and added initial supporting hardware
    [SDP.kicad_pcb, SDP.kicad_sch]
2022-01-27 Added stepper motor driver
    [filtersubsystem.kicad_sch]
2022-01-27 PIC24 pins
    [PIC24_pins.xlsx]
2022-01-27 Added sheet
    [SDP.kicad_sch, filtersubsystem.kicad_sch, grindersubsystem.kicad_sch]
2022-01-27 Added datasheets and schematics
2022-01-28 Updated schematics
    [PIC24_pins.xlsx, SDP.kicad_sch, watersubsystem.kicad_sch]
2022-02-03 Added DS3231 RTC and HM-10 BLE module
    [SDP.kicad_sch, brewingsubsystem.kicad_sch, filtersubsystem.kicad_sch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]
2022-02-04 Added 5V and 3.3V voltage regulators
    [SDP.kicad_sch, power.xlsx]
2022-02-04 Updated power section
    [SDP.kicad_sch]
2022-02-04 Updated power requirement estimates
    [power.xlsx]
2022-02-05 Added GPIO headers, separated power PCB
    [SDP.kicad_sch, SDP_power.kicad_pcb, SDP_power.kicad_sch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]
2022-02-05 Updated pin assignments
    [PIC24_pins.xlsx]
2022-02-05 Updated power estimates
    [power.xlsx]
2022-02-07 Part selection
    [SDP.kicad_sch, brewingsubsystem.kicad_sch, filtersubsystem.kicad_sch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]
2022-02-08 Added footprints
    [SDP.kicad_sch, brewingsubsystem.kicad_sch, filtersubsystem.kicad_sch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]
2022-02-09 Assigned footprints, added limit switches, rearranged schematics
    [SDP.kicad_sch, brewingsubsystem.kicad_sch, filtersubsystem.kicad_sch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]
2022-02-10 Assigned footprints and removed ferrite bead
    [SDP.kicad_sch, sensors.kicad_sch, steppermotors.kicad_sch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]
2022-02-10 Added MCLR pullup and assigned footprints
    [SDP.kicad_sch, steppermotors.kicad_sch]
2022-02-10 Added input filter and power headers
    [SDP.kicad_sch, steppermotors.kicad_sch]
2022-02-13 PCB layout and footprint assignment fix
    [SDP.kicad_pcb, SDP.kicad_sch, SDP_power.kicad_sch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]
2022-02-14 PCB layout and schematic updates
    [SDP.kicad_pcb, SDP.kicad_sch, sensors.kicad_sch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]
2022-02-14 Added limit switches
    [PIC24_pins.xlsx]
2022-02-14 Separated control and motor boards
    [SDP.kicad_pcb, SDP.kicad_sch, SDP_motors.kicad_pcb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]
2022-02-16 PCB layout of main controller board
    [SDP.kicad_pcb, SDP.kicad_sch]
2022-02-16 Controller PCB layout
    [SDP.kicad_pcb, SDP.kicad_sch, sensors.kicad_sch]
2022-02-17 Modified TOF sensor pins
    [PIC24_pins.xlsx]
2022-02-18 Added proximity sensor headers
    [SDP.kicad_pcb, SDP.kicad_sch, SDP_motors.kicad_pcb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]
2022-02-21 Motor PCB layout
    [SDP.kicad_pcb, SDP.kicad_sch, SDP_motors.kicad_pcb]
2022-02-21 Controller and motor PCB silkscreen and final layout
    [SDP.kicad_pcb, SDP.kicad_sch, SDP_motors.kicad_pcb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]
2022-02-24 Final PCB layout changes
    [SDP-B_Cu.gbr, SDP-B_Mask.gbr, SDP-B_Paste.gbr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]
2022-03-03 Added proximity sensor pins
    [PIC24_pins.xlsx]

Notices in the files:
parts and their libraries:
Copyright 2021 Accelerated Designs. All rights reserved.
